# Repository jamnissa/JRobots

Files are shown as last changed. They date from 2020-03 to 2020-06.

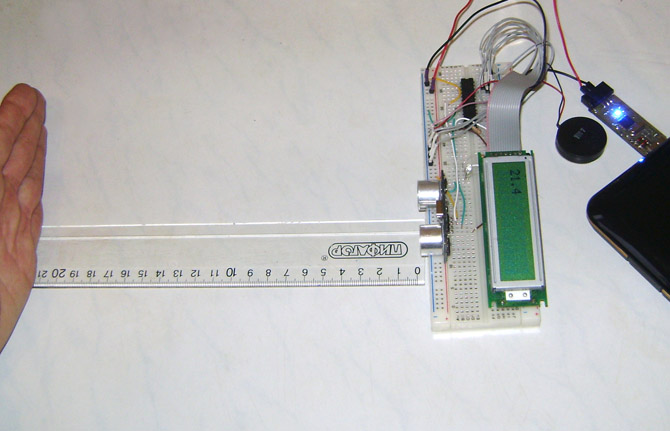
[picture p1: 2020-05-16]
Trash/21sm.jpg

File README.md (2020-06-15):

### JRobots

#### Структура проекта
- [pcbDocuments](pcbDocuments)
    - [pcbDocuments.dwg](pcbDocuments/pcbDocuments.dwg)
    - [Схема электрическая структурная](pcbDocuments/pdfDocuments/E1.pdf)
    - [Схема электрическая функциональная](pcbDocuments/pdfDocuments/E2.pdf)
    - [Схема электрическая принципиальная](pcbDocuments/pdfDocuments/E3.pdf)
    - [Перечень элементов](pcbDocuments/pdfDocuments/PE3.pdf)
    - [Печатная плата](pcbDocuments/pdfDocuments/PP.pdf)
    - [Сборочный чертеж ячейки](pcbDocuments/pdfDocuments/SB.pdf)
    - [Спецификация](pcbDocuments/pdfDocuments/Spec.pdf)
    - [Сборочный чертеж корпуса](pcbDocuments/pdfDocuments/SB_corpus.pdf)
    - [Спецификация 2](pcbDocuments/pdfDocuments/Spec_corpus.pdf)
    - [Алгоритм](pcbDocuments/pdfDocuments/Algoritm.pdf)
    - [Схема сборки](pcbDocuments/pdfDocuments/Sborka.pdf)
    - [Исследовательский лист](pcbDocuments/pdfDocuments/Search.pdf)
    - [Исследовательский лист2](pcbDocuments/pdfDocuments/Search2.pdf)

- [pcbBoard](pcbBoard)
    - [Robot.PrjPcb](pcbBoard/Robot.PrjPcb)
    - [Schematic.SchDoc](pcbBoard/Schematic.SchDoc)
    - [PcbBoard.PcbDoc](pcbBoard/PcbBoard_last3.PcbDoc)
    
- [pcbCase](pcbCase)
    - [ball.ipt](pcbCase/ball/ball.iam)
    - [battery case.ipt](pcbCase/case18650/case18650.ipt)
    - [fixation for motor.ipt](pcbCase/soporte_plastico/soporte_plastico.ipt)
    - [lidar.ipt](pcbCase/lidar/lidar.ipt)
    - [wheel.ipt](pcbCase/wheel/Wheel.ipt)
    - [motor.ipt](pcbCase/motor/motor.ipt)
    - [sborka](pcbCase/pcbCase/sborka.iam)

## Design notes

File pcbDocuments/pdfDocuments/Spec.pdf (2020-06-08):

Инв. №подл Подп. и Дата Взам.инв.№ Инв.№ дубл. Подп. и Дата Справ № Перв. примен. Изм. Лист № докум. Лит. Листов МГТУ им. Н.Э.Баумана Кафедра ИУ4 Группа ИУ4-81Б Лист Робот

-транспортер Спецификация Подпись | Дата Разраб. Пров. Реценз. Н.контр. Утв. | Исабаева Ж. | ИУ4.11.03.03.20.81.06.005 СП
1 | 2 | Инв. №подл Подп. и Дата Взам.инв.№ Инв.№ дубл. Подп. и Дата Справ № Перв. примен. | Изм. | Лист | № докум. | Подпись | Дата | Лист
2 ИУ4.11.03.03.20.81.06.005 СП Копировал | Формат A4 | Копировал | Формат A4

Форм. Зона

## Поз. Обозначение Наименование

Кол. Примечание ИУ4.11.03.03.20.81.06.004 Печатная плата Документация A2 Сборочный чертеж ячейки 1 A2 ИУ4.11.03.03.20.81.06.001

Э1 | Схема электрическая структурная A1 | ИУ4.11.03.03.20.81.06.003
Э3 | Схема электрическая принципиальная A4 | ИУ4.11.03.03.20.81.06.003 ПЭ3 | Перечень элементов A2 | ИУ4.11.03.03.20.81.06.004 | Чертеж печатной платы

1

1

1

1

1

Форм. Зона

## Поз. Обозначение Наименование

Кол. Примечание

1

1 | C8-C13,C16,C19 | Светодиод TO-2013BC, 0805 CC2541 BluetoothмодульJDY-08 STM32F103C8T6, [LQFP-48] | VD1 DD2
1 Светодиоды Микросхемы | DD1
1 PH2.0-2Вилка прямая на плату | 1 | XP1 Разъемы PLD6 Вилка прямая на плату | XP2 TB6612FNG [SSOP-24] | DD3 AMS1117-3.3, [SOT-223] | DA1 AMS1117-5, [SOT-223] | DA2
1 PH2.0-4Вилка прямая на плату | XP3 PH1.5-6,Вилка прямая на плату | 2 | XP4,XP5 Кнопка с фиксацией PS700L | SW1 Переключатели Кнопка тактовая KLS7-TS6601 | SW2 Дроссель подавления ЭМП, | 1 | L1 Катушки индуктивности

1

1

1

1

1

1 BLM21BD182SN1D,0805 Копировал | Формат A4 HC-49SM, 8МГц | 1 | ZQ1 Кварцевые резонаторы Кер.ЧИП конд.0,1мкФ,50
В,0805 | 11 | C1,C3,C5, Конденсаторы ECAP SMD 220мкФ,16
В Кер.ЧИП конд.22пФ,250 | 4
В,0805 В,0805 Кер.ЧИП конд.1мкФ,16 | 2 | C2,C4,C14,C18 C6,C7 C15 C17
В,0805 Кер.ЧИП конд.2,2мкФ.16 | 1

1

3 ЧИП резистор 4,7кОм,0805 2 1 1 1 | R4-R6 Биполярный транзистор PNP, R2,R3 ЧИП резистор 4,7кОм, 0805 VT1 Транзисторы SOT-23 Пьезоэлектрический излучатель BQ1 Преобразователи пассивный HPM14A, 5 R1 Резисторы ЧИП резистор 1кОм,0805

В Детали Прочие изделия ИУ4.11.03.03.20.81.06.005 СБ Артемьев Б.В. Сергеева М.Д.

ВЫПОЛНЕНО В СТУДЕНЧЕСКОЙ ВЕРСИИ ПРОГРАММЫ AUTODESK ВЫПОЛНЕНО В СТУДЕНЧЕСКОЙ ВЕРСИИ ПРОГРАММЫ AUTODESK

ВЫПОЛНЕНО В СТУДЕНЧЕСКОЙ ВЕРСИИ ПРОГРАММЫ AUTODESK ВЫПОЛНЕНО В СТУДЕНЧЕСКОЙ ВЕРСИИ ПРОГРАММЫ AUTODESK

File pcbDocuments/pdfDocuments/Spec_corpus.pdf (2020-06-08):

Инв. №подл Подп. и Дата Взам.инв.№ Инв.№ дубл. Подп. и Дата Справ № Перв. примен. Изм. Лист № докум. Лит. Листов МГТУ им. Н.Э.Баумана Кафедра ИУ4 Группа ИУ4-81Б Лист Робот

-транспортер Спецификация 2 Подпись | Дата Разраб. Пров. Реценз. Н.контр. Утв. | Исабаева Ж. | ИУ4.11.03.03.20.81.06.006СП
1 | 2 | Инв. №подл Подп. и Дата Взам.инв.№ Инв.№ дубл. Подп. и Дата Справ № Перв. примен. | Изм. | Лист | № докум. | Подпись | Дата | Лист
2 ИУ4.11.03.03.20.81.06.006СП Копировал | Формат A4 | Копировал | Формат A4

Форм. Зона

## Поз. Обозначение Наименование

Кол. Примечание Детали ИУ4.11.03.03.20.81.06.004 Печатная плата Документация A2 ИУ4.11.03.03.20.81.06.007 СБ Сборочный чертеж устройства 1 A2 ИУ4.11.03.03.20.81.06.001

Э1 | Схема электрическая структурная A1 | ИУ4.11.03.03.20.81.06.003
ИУ4.11.03.03.20.81.06.003 ПЭ3 ИУ4.11.03.03.20.81.06.004 Э3 | Схема электрическая принципиальная A4 Перечень элементов A2 Чертеж печатной платы | 1
| | 1

1

1 Прочие изделия

1 2 | Кронштейн для двигателя Инкрементный энкодер ЭлектродвигательGA12-N20 | 1
34 | | 1
| | 2 Верхняя крышка Нижняя крышка Верхнее основание Колесо 12
7 | 2
8 | 2

9

Форм. Зона

## Поз. Обозначение Наименование

Кол. Примечание

1

5 | 1618

1

6 | Шаровая опора Pololu 3/8" | 2 10 | Батарейный отсек 2х18650 | 1 Стойка для печатных плат, HTP-325 11 | Винт с круглой головкой
4 1213 | Лидар TF-mini | Винт с потайной головкой

8

7 | 15 15 Стойка для печатных плат, HTS-325 14 | 1 Кронштейн для лидара | M3x10 M2x4 Винт с круглой головкой | 2 17 | Винт с потайной головкой
8 M2x5 19 | Гайка M2 | 14 M2x10 A2 | ИУ4.11.03.03.20.81.06.005 СБ | Сборочный чертеж ячейки | 1 Артемьев Б.В. Сергеева М.Д.

ВЫПОЛНЕНО В СТУДЕНЧЕСКОЙ ВЕРСИИ ПРОГРАММЫ AUTODESK ВЫПОЛНЕНО В СТУДЕНЧЕСКОЙ ВЕРСИИ ПРОГРАММЫ AUTODESK

ВЫПОЛНЕНО В СТУДЕНЧЕСКОЙ ВЕРСИИ ПРОГРАММЫ AUTODESK ВЫПОЛНЕНО В СТУДЕНЧЕСКОЙ ВЕРСИИ ПРОГРАММЫ AUTODESK

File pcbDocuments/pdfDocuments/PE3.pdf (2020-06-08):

Инв. №подл Подп. и Дата Взам.инв.№ Инв.№ дубл. Подп. и Дата Справ № Перв. примен. Изм. Лист № докум.

ЗонаПоз. Обозна
-чение | Обозначение

# Кол. Примечание Лит. Листов 1 МГТУ им. Н.Э.Баумана Кафедра ИУ4 Группа ИУ4-81Б Лист Робот

-транспортер Перечень элементов Подпись | Дата Разраб. Пров. Реценз. Н.контр. Утв. | ИУ4.11.03.03.20.81.06.003 ПЭ

3

1 | 2 | Инв. №подл Подп. и Дата Взам.инв.№ Инв.№ дубл. Подп. и Дата Справ № Перв. примен. | Зона | Поз. Обозна
-чение | Обозначение

Кол. Примечание Изм. Лист № докум. Подпись Дата Лист

## 2 ИУ4.11.03.03.20.81.06.003 ПЭ

3 Светодиод желтый TO-2013BC-MYF, 0805, КНР CC2541 Bluetoothмодуль JDY-08, Texas Instruments STM32F103C8T6,32-Бит,Cortex-M3, 72 МГц, | VD1 DD2 | Светодиоды Микросхемы DD1 | 1 Конденсаторы Кер.ЧИП конд.0,1мкФ±10% 50

В-X7R-0805 EGRM21BR71H104K, Murata Manufacturing ECAP SMD 220мкФ±20%-16 В-Y5V-6,3x7,7 C1,C3,C5 C2,C4,C14 C18

1 XP1 | PH2.0-2, Вилка прямая на плату 2.0мм, КНР | 1 Разъемы XP2 | PLD6 Вилка прямая на плату, Тайвань Копировал | Формат A4 | Копировал | Формат A4 Копировал | Формат A4

1 Кер.ЧИП конд.22пФ±5% 250

Кер.ЧИП конд.2,2мкФ±10% 16 В-C0G-0805 GRM21A5C2E220J, Murata Manufacturing C6,C7 C15 | 2 Кер.ЧИП конд. 1мкФ±10% 16
В-Y5V-0805,Тайвань | 1 64 КБ Flash [LQFP-48], Швейцария DD3 | TB6612FNG [SSOP-24],Toshiba,Япония | 1 DA1 | AMS1117-3.3,Линейный стабилизатор[SOT-223],3.3
AMS1117-5,Линейный стабилизатор [SOT-223],5 В,КНР | 1 DA2
В,КНР | 1
1 XP3 | PH2.0-4, Вилка прямая на плату 2.0мм, КНР | XP4,XP5 | PH1.5-6, Вилка прямая на плату 1.5мм, КНР | 2 BQ1 | Пьезоэлектрический излучатель пассивный HPM14A, 5
В | 1 Кварцевые резонаторы | SW1 | Кнопка с фиксацией PS700L, КНР | 1 Переключатели C17 | SW2 | Кнопка тактовая KLS7-TS6601-5.0 | 1 ZQ1 | HC-49SM 8МГц,КНР | 1 L1 | Дроссель подавления ЭМП,BLM21BD182SN1D,1.8кОм,0805 | 1 Катушки индуктивности C8-C13, C16,C19 | 114
В-X7R-0805 | 1
3 R1 | ЧИП резистор 4,7кОм± 5%-0,125-0805, Тайвань | 1 Резисторы R2,R3 | ЧИП резистор 1кОм± 5%-0,125-0805, Тайвань | 2 R4-R6 | ЧИП резистор 4,7кОм± 5%-0,125-0805, Тайвань
1 VT1 | Биполярный транзистор PNP SOT-23,KTC9012S-H-RTK/P | 1 Транзисторы Преобразователи Исабаева Ж. Сергеева М.Д. Артемьев Б.В. ВЫПОЛНЕНО В СТУДЕНЧЕСКОЙ ВЕРСИИ ПРОГРАММЫ AUTODESK | ВЫПОЛНЕНО В СТУДЕНЧЕСКОЙ ВЕРСИИ ПРОГРАММЫ AUTODESK

ВЫПОЛНЕНО В СТУДЕНЧЕСКОЙ ВЕРСИИ ПРОГРАММЫ AUTODESK ВЫПОЛНЕНО В СТУДЕНЧЕСКОЙ ВЕРСИИ ПРОГРАММЫ AUTODESK

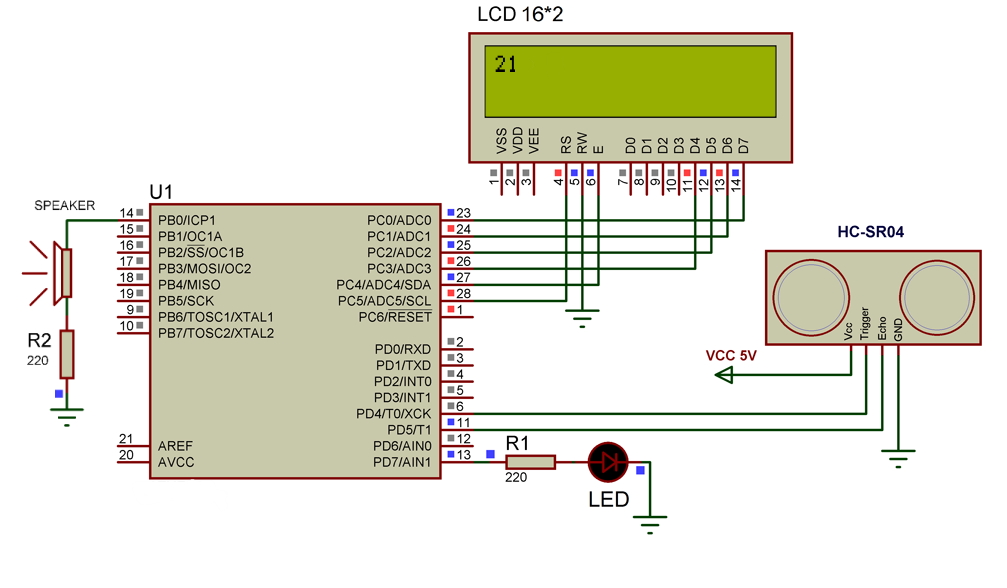
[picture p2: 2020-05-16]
Trash/proteus.jpg

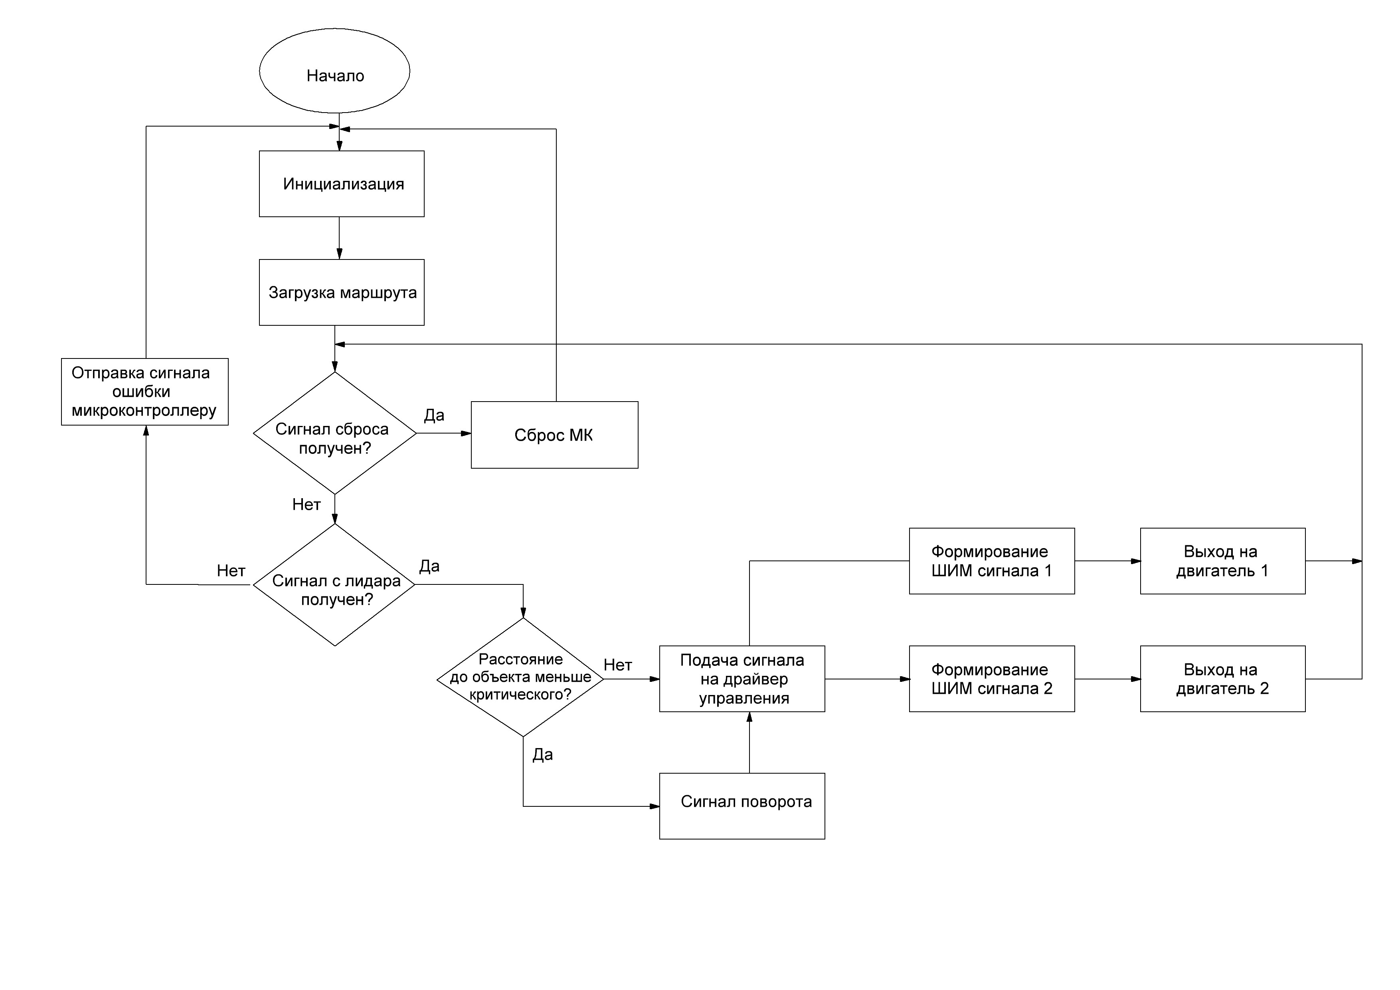
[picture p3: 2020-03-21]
Trash/алгоритм.JPG

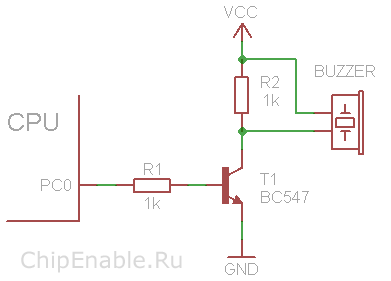
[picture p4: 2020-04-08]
Trash/buzzer3.png

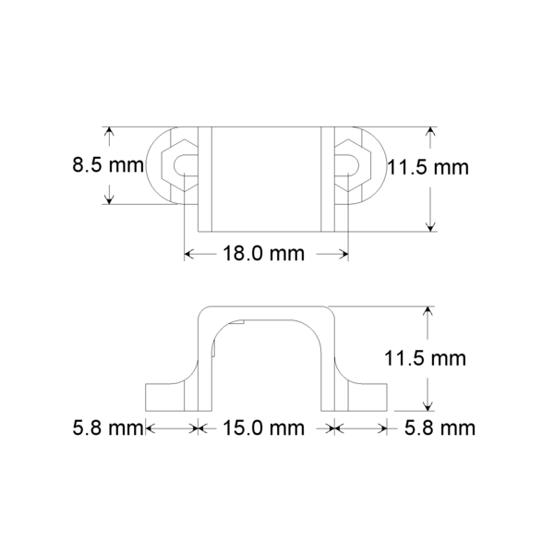
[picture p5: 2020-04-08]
Trash/19a99f53-5988-11e1-8759-001d60b84a57_5c161ac9-bea5-11e1-bbff-001d60b84a57.resize1.jpeg

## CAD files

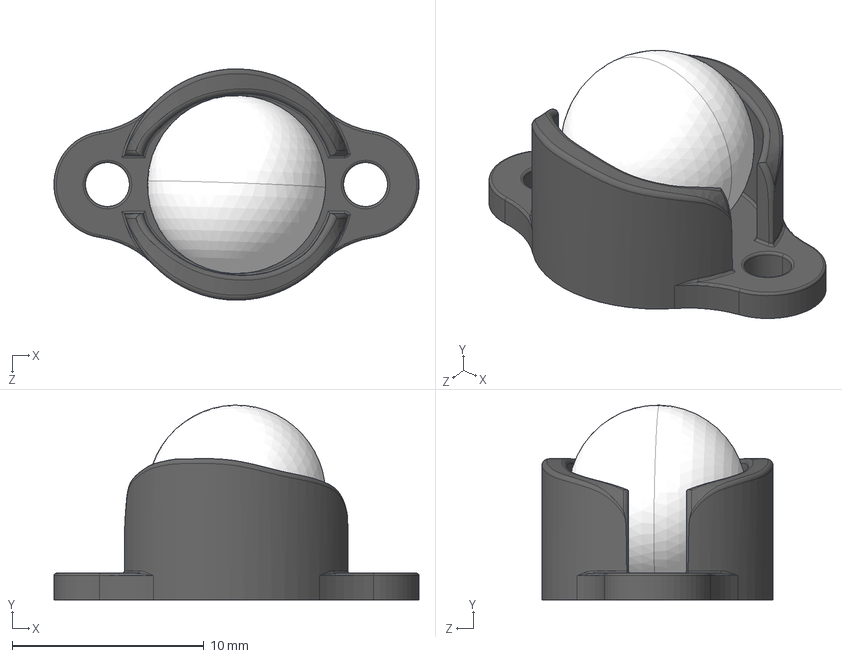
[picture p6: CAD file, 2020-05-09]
pcbCase/ball/ball.STEP
19.0 x 10.2 x 12.1 mm
base
ball

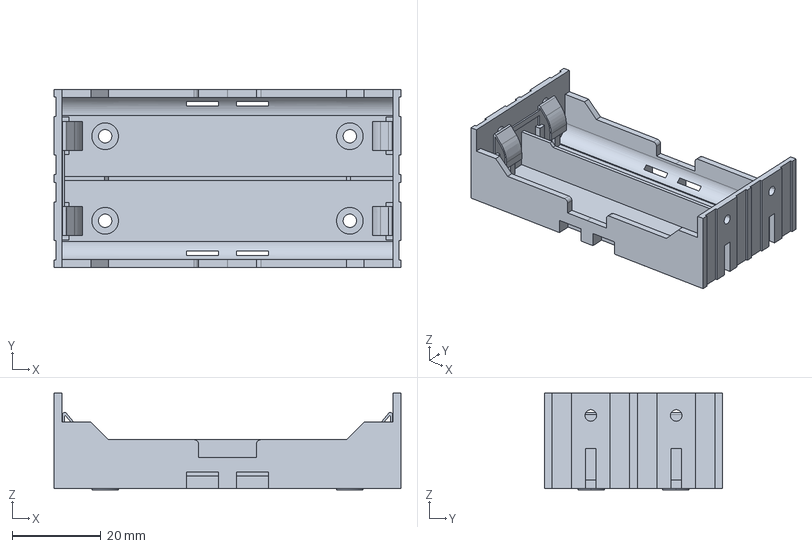
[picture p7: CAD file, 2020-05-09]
pcbCase/case18650/case18650.stp
78.0 x 40.0 x 21.8 mm

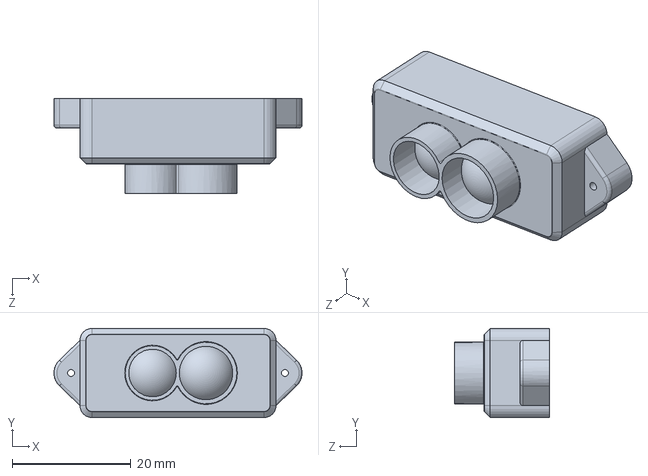
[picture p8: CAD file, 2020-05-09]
pcbCase/lidar/mini_Lidar.SLDPRT
41.7 x 15.0 x 16.0 mm

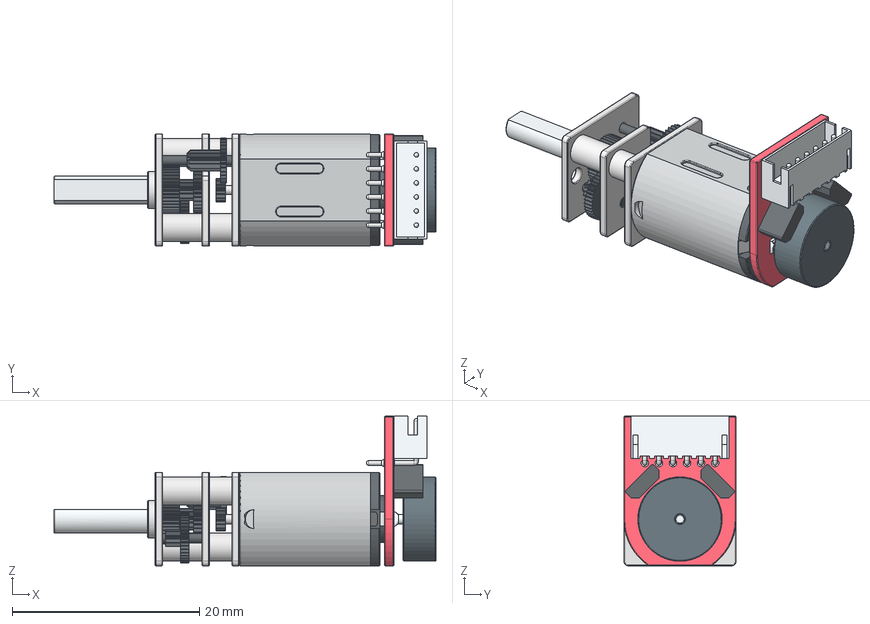
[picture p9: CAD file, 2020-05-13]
pcbCase/motor/motor.stp
40.8 x 12.0 x 16.0 mm
motor_1
motor_1_1
motor_2
motor_3
motor_4
motor_5
motor_6
motor_7
motor_8
motor_9
motor_10
motor_11
motor_12
motor_13
motor_14
motor_15
motor_16
motor_17
motor_18
motor_19
motor_20
motor_21
motor_22
motor_23
motor_24
motor_25
motor_26
motor_27
motor_28
motor_29
motor_30
motor_31
motor_32
motor_33
motor_34
motor_35
motor_36

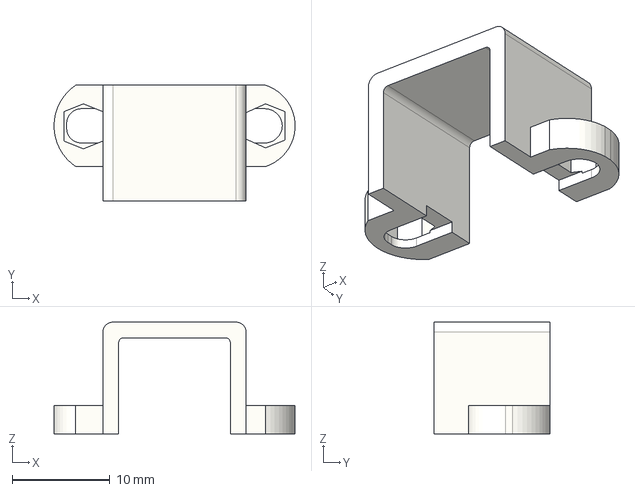
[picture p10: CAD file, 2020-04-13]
pcbCase/soporte_plastico/soporte_plastico.step
24.6 x 11.8 x 11.4 mm

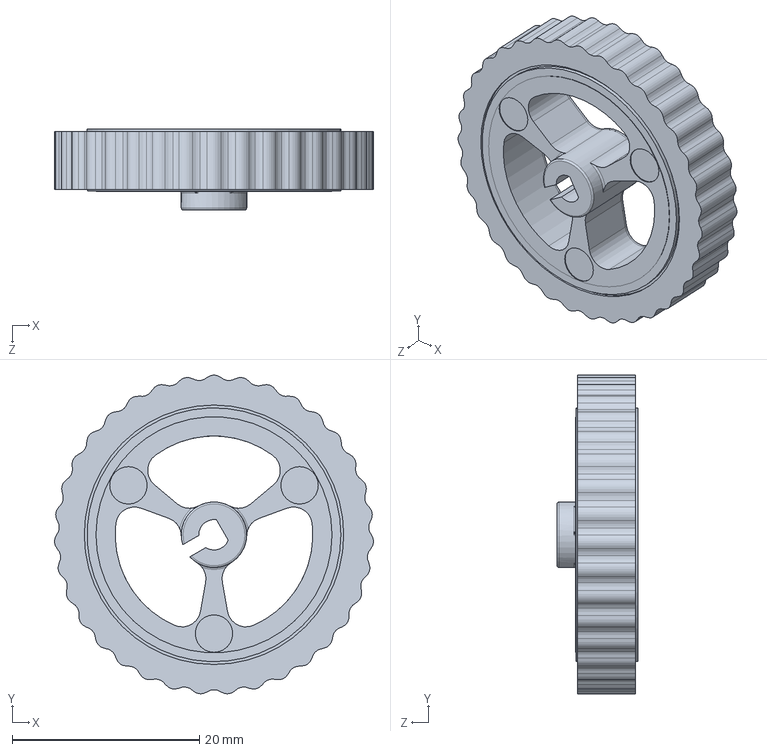
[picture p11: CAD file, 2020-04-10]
pcbCase/wheel/Wheel.SLDPRT
34.1 x 34.0 x 8.65 mm

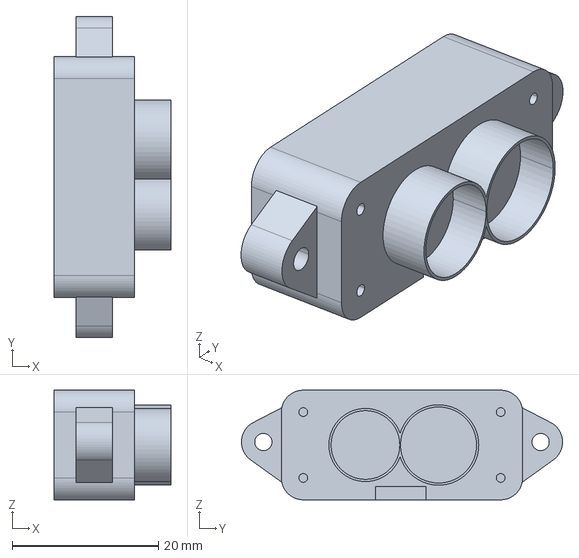
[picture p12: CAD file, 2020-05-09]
pcbCase/lidar/lidar.stp
16.0 x 43.9 x 15.0 mm

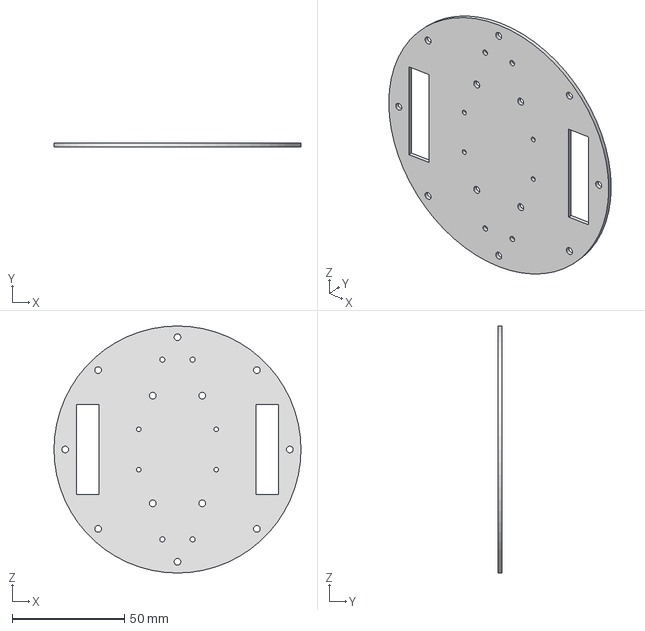
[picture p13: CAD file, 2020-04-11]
pcbCase/pcbCase/pcbCase.stp
110.0 x 1.60 x 110.0 mm

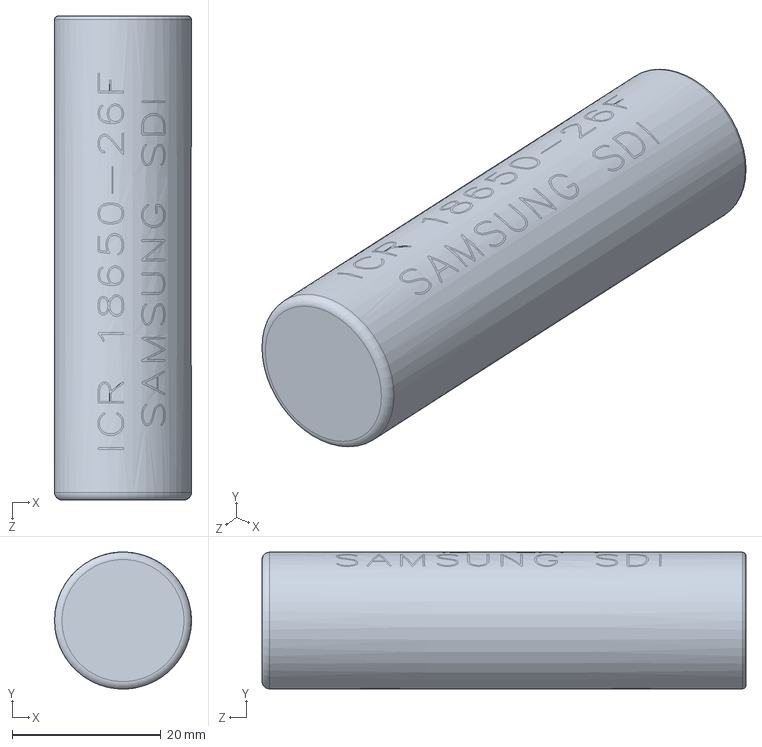
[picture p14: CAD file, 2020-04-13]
pcbCase/case18650/18650.SLDPRT
18.4 x 18.4 x 65.0 mm

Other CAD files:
pcbCase/pcbCase/caseTop.dwg
pcbDocuments/pcbDocuments.dwg
pcbCase/pcbCase/pcbCase_last.dwg
pcbDocuments/pcbDoc.dwg
pcbCase/case18650/BatteryCase.dwg
pcbCase/pcbCase/caseBottom.dwg
pcbCase/pcbCase/Board.dwg
pcbCase/OldVersions/sborka2.0001.dwg
pcbCase/pcbCase/OldVersions/caseBottom.0002.dwg
pcbCase/Board/0805LED-red.ipt
pcbCase/Board/B6B-ZR.ipt
pcbCase/Board/BQ1.iam
pcbCase/Board/BQ2.iam
pcbCase/Board/Board.iam
pcbCase/Board/C1.iam
pcbCase/Board/C10.iam
pcbCase/Board/C11.iam
pcbCase/Board/C12.iam
pcbCase/Board/C13.iam
pcbCase/Board/C14.iam
pcbCase/Board/C15.iam
pcbCase/Board/C16.iam
pcbCase/Board/C17.iam
pcbCase/Board/C18.iam
pcbCase/Board/C19.iam
pcbCase/Board/C2.iam
pcbCase/Board/C3.iam
pcbCase/Board/C4.iam
pcbCase/Board/C5.iam
pcbCase/Board/C6.iam
pcbCase/Board/C7.iam
pcbCase/Board/C8.iam
pcbCase/Board/C9.iam
pcbCase/Board/DA1.iam
pcbCase/Board/DA2.iam
pcbCase/Board/DD1.iam
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

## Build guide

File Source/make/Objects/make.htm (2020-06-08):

# Static Call Graph for image .\Objects\make.axf

#<CALLGRAPH># ARM Linker, 5060750: Last Updated: Sun Jun 07 21:56:51 2020

### Maximum Stack Usage = 96 bytes + Unknown(Functions without stacksize, Cycles, Untraceable Function Pointers)

### Call chain for Maximum Stack Depth:

TIM4_IRQHandler ⇒ encoderRead ⇒ __aeabi_dmul

### Functions with no stack information

- __user_initial_stackheap

### Mutually Recursive functions

- NMI_Handler ⇒ NMI_Handler
- HardFault_Handler ⇒ HardFault_Handler
- MemManage_Handler ⇒ MemManage_Handler
- BusFault_Handler ⇒ BusFault_Handler
- UsageFault_Handler ⇒ UsageFault_Handler
- SVC_Handler ⇒ SVC_Handler
- DebugMon_Handler ⇒ DebugMon_Handler
- PendSV_Handler ⇒ PendSV_Handler
- SysTick_Handler ⇒ SysTick_Handler
- ADC1_2_IRQHandler ⇒ ADC1_2_IRQHandler

### Function Pointers

- ADC1_2_IRQHandler from startup_stm32f10x_md.o(.text) referenced from startup_stm32f10x_md.o(RESET)
- BusFault_Handler from startup_stm32f10x_md.o(.text) referenced from startup_stm32f10x_md.o(RESET)
- CAN1_RX1_IRQHandler from startup_stm32f10x_md.o(.text) referenced from startup_stm32f10x_md.o(RESET)
- CAN1_SCE_IRQHandler from startup_stm32f10x_md.o(.text) referenced from startup_stm32f10x_md.o(RESET)
- DMA1_Channel1_IRQHandler from startup_stm32f10x_md.o(.text) referenced from startup_stm32f10x_md.o(RESET)
- DMA1_Channel2_IRQHandler from startup_stm32f10x_md.o(.text) referenced from startup_stm32f10x_md.o(RESET)
- DMA1_Channel3_IRQHandler from startup_stm32f10x_md.o(.text) referenced from startup_stm32f10x_md.o(RESET)
- DMA1_Channel4_IRQHandler from startup_stm32f10x_md.o(.text) referenced from startup_stm32f10x_md.o(RESET)
- DMA1_Channel5_IRQHandler from startup_stm32f10x_md.o(.text) referenced from startup_stm32f10x_md.o(RESET)
- DMA1_Channel6_IRQHandler from startup_stm32f10x_md.o(.text) referenced from startup_stm32f10x_md.o(RESET)
- DMA1_Channel7_IRQHandler from startup_stm32f10x_md.o(.text) referenced from startup_stm32f10x_md.o(RESET)
- DebugMon_Handler from startup_stm32f10x_md.o(.text) referenced from startup_stm32f10x_md.o(RESET)
- EXTI0_IRQHandler from startup_stm32f10x_md.o(.text) referenced from startup_stm32f10x_md.o(RESET)
- EXTI15_10_IRQHandler from startup_stm32f10x_md.o(.text) referenced from startup_stm32f10x_md.o(RESET)
- EXTI1_IRQHandler from startup_stm32f10x_md.o(.text) referenced from startup_stm32f10x_md.o(RESET)
- EXTI2_IRQHandler from startup_stm32f10x_md.o(.text) referenced from startup_stm32f10x_md.o(RESET)
- EXTI3_IRQHandler from startup_stm32f10x_md.o(.text) referenced from startup_stm32f10x_md.o(RESET)
- EXTI4_IRQHandler from startup_stm32f10x_md.o(.text) referenced from startup_stm32f10x_md.o(RESET)
- EXTI9_5_IRQHandler from startup_stm32f10x_md.o(.text) referenced from startup_stm32f10x_md.o(RESET)
- FLASH_IRQHandler from startup_stm32f10x_md.o(.text) referenced from startup_stm32f10x_md.o(RESET)
- HardFault_Handler from startup_stm32f10x_md.o(.text) referenced from startup_stm32f10x_md.o(RESET)
- I2C1_ER_IRQHandler from startup_stm32f10x_md.o(.text) referenced from startup_stm32f10x_md.o(RESET)
- I2C1_EV_IRQHandler from startup_stm32f10x_md.o(.text) referenced from startup_stm32f10x_md.o(RESET)
- I2C2_ER_IRQHandler from startup_stm32f10x_md.o(.text) referenced from startup_stm32f10x_md.o(RESET)
- I2C2_EV_IRQHandler from startup_stm32f10x_md.o(.text) referenced from startup_stm32f10x_md.o(RESET)
- MemManage_Handler from startup_stm32f10x_md.o(.text) referenced from startup_stm32f10x_md.o(RESET)
- NMI_Handler from startup_stm32f10x_md.o(.text) referenced from startup_stm32f10x_md.o(RESET)
- PVD_IRQHandler from startup_stm32f10x_md.o(.text) referenced from startup_stm32f10x_md.o(RESET)
- PendSV_Handler from startup_stm32f10x_md.o(.text) referenced from startup_stm32f10x_md.o(RESET)
- RCC_IRQHandler from startup_stm32f10x_md.o(.text) referenced from startup_stm32f10x_md.o(RESET)
- RTCAlarm_IRQHandler from startup_stm32f10x_md.o(.text) referenced from startup_stm32f10x_md.o(RESET)
- RTC_IRQHandler from startup_stm32f10x_md.o(.text) referenced from startup_stm32f10x_md.o(RESET)
- Reset_Handler from startup_stm32f10x_md.o(.text) referenced from startup_stm32f10x_md.o(RESET)
- SPI1_IRQHandler from startup_stm32f10x_md.o(.text) referenced from startup_stm32f10x_md.o(RESET)
- SPI2_IRQHandler from startup_stm32f10x_md.o(.text) referenced from startup_stm32f10x_md.o(RESET)
- SVC_Handler from startup_stm32f10x_md.o(.text) referenced from startup_stm32f10x_md.o(RESET)
- SysTick_Handler from startup_stm32f10x_md.o(.text) referenced from startup_stm32f10x_md.o(RESET)
- SystemInit from system_stm32f10x.o(i.SystemInit) referenced from startup_stm32f10x_md.o(.text)
- TAMPER_IRQHandler from startup_stm32f10x_md.o(.text) referenced from startup_stm32f10x_md.o(RESET)
- TIM1_BRK_IRQHandler from startup_stm32f10x_md.o(.text) referenced from startup_stm32f10x_md.o(RESET)
- TIM1_CC_IRQHandler from startup_stm32f10x_md.o(.text) referenced from startup_stm32f10x_md.o(RESET)
- TIM1_TRG_COM_IRQHandler from startup_stm32f10x_md.o(.text) referenced from startup_stm32f10x_md.o(RESET)
- TIM1_UP_IRQHandler from startup_stm32f10x_md.o(.text) referenced from startup_stm32f10x_md.o(RESET)
- TIM2_IRQHandler from startup_stm32f10x_md.o(.text) referenced from startup_stm32f10x_md.o(RESET)
- TIM3_IRQHandler from startup_stm32f10x_md.o(.text) referenced from startup_stm32f10x_md.o(RESET)
- TIM4_IRQHandler from jrobot.o(i.TIM4_IRQHandler) referenced from startup_stm32f10x_md.o(RESET)
- USART1_IRQHandler from startup_stm32f10x_md.o(.text) referenced from startup_stm32f10x_md.o(RESET)
- USART2_IRQHandler from startup_stm32f10x_md.o(.text) referenced from startup_stm32f10x_md.o(RESET)
- USART3_IRQHandler from startup_stm32f10x_md.o(.text) referenced from startup_stm32f10x_md.o(RESET)
- USBWakeUp_IRQHandler from startup_stm32f10x_md.o(.text) referenced from startup_stm32f10x_md.o(RESET)
- USB_HP_CAN1_TX_IRQHandler from startup_stm32f10x_md.o(.text) referenced from startup_stm32f10x_md.o(RESET)
- USB_LP_CAN1_RX0_IRQHandler from startup_stm32f10x_md.o(.text) referenced from startup_stm32f10x_md.o(RESET)
- UsageFault_Handler from startup_stm32f10x_md.o(.text) referenced from startup_stm32f10x_md.o(RESET)
- WWDG_IRQHandler from startup_stm32f10x_md.o(.text) referenced from startup_stm32f10x_md.o(RESET)
- __main from __main.o(!!!main) referenced from startup_stm32f10x_md.o(.text)

### Global Symbols

__main (Thumb, 8 bytes, Stack size 0 bytes, __main.o(!!!main))

[Calls]

- >> __scatterload
- >> __rt_entry

__scatterload (Thumb, 0 bytes, Stack size unknown bytes, __scatter.o(!!!scatter))

[Called By]

- >> __main

__scatterload_rt2 (Thumb, 44 bytes, Stack size unknown bytes, __scatter.o(!!!scatter), UNUSED)

[Calls]

- >> __rt_entry

__scatterload_rt2_thumb_only (Thumb, 0 bytes, Stack size unknown bytes, __scatter.o(!!!scatter), UNUSED)

__scatterload_null (Thumb, 0 bytes, Stack size unknown bytes, __scatter.o(!!!scatter), UNUSED)

__scatterload_copy (Thumb, 26 bytes, Stack size unknown bytes, __scatter_copy.o(!!handler_copy), UNUSED)

[Calls]

- >> __scatterload_copy

[Called By]

- >> __scatterload_copy

__scatterload_zeroinit (Thumb, 28 bytes, Stack size unknown bytes, __scatter_zi.o(!!handler_zi), UNUSED)

__rt_lib_init (Thumb, 0 bytes, Stack size unknown bytes, libinit.o(.ARM.Collect$$libinit$$00000000))

[Called By]

- >> __rt_entry_li

__rt_lib_init_alloca_1 (Thumb, 0 bytes, Stack size unknown bytes, libinit2.o(.ARM.Collect$$libinit$$0000002E))

__rt_lib_init_argv_1 (Thumb, 0 bytes, Stack size unknown bytes, libinit2.o(.ARM.Collect$$libinit$$0000002C))

__rt_lib_init_atexit_1 (Thumb, 0 bytes, Stack size unknown bytes, libinit2.o(.ARM.Collect$$libinit$$0000001B))

__rt_lib_init_clock_1 (Thumb, 0 bytes, Stack size unknown bytes, libinit2.o(.ARM.Collect$$libinit$$00000021))

__rt_lib_init_cpp_1 (Thumb, 0 bytes, Stack size unknown bytes, libinit2.o(.ARM.Collect$$libinit$$00000032))

__rt_lib_init_exceptions_1 (Thumb, 0 bytes, Stack size unknown bytes, libinit2.o(.ARM.Collect$$libinit$$00000030))

__rt_lib_init_fp_1 (Thumb, 0 bytes, Stack size unknown bytes, libinit2.o(.ARM.Collect$$libinit$$00000002))

__rt_lib_init_fp_trap_1 (Thumb, 0 bytes, Stack size unknown bytes, libinit2.o(.ARM.Collect$$libinit$$0000001F))

__rt_lib_init_getenv_1 (Thumb, 0 bytes, Stack size unknown bytes, libinit2.o(.ARM.Collect$$libinit$$00000023))

__rt_lib_init_heap_1 (Thumb, 0 bytes, Stack size unknown bytes, libinit2.o(.ARM.Collect$$libinit$$0000000A))

__rt_lib_init_lc_collate_1 (Thumb, 0 bytes, Stack size unknown bytes, libinit2.o(.ARM.Collect$$libinit$$00000011))

__rt_lib_init_lc_ctype_1 (Thumb, 0 bytes, Stack size unknown bytes, libinit2.o(.ARM.Collect$$libinit$$00000013))

__rt_lib_init_lc_monetary_1 (Thumb, 0 bytes, Stack size unknown bytes, libinit2.o(.ARM.Collect$$libinit$$00000015))

__rt_lib_init_lc_numeric_1 (Thumb, 0 bytes, Stack size unknown bytes, libinit2.o(.ARM.Collect$$libinit$$00000017))

__rt_lib_init_lc_time_1 (Thumb, 0 bytes, Stack size unknown bytes, libinit2.o(.ARM.Collect$$libinit$$00000019))

__rt_lib_init_preinit_1 (Thumb, 0 bytes, Stack size unknown bytes, libinit2.o(.ARM.Collect$$libinit$$00000004))

__rt_lib_init_rand_1 (Thumb, 0 bytes, Stack size unknown bytes, libinit2.o(.ARM.Collect$$libinit$$0000000E))

__rt_lib_init_return (Thumb, 0 bytes, Stack size unknown bytes, libinit2.o(.ARM.Collect$$libinit$$00000033))

__rt_lib_init_signal_1 (Thumb, 0 bytes, Stack size unknown bytes, libinit2.o(.ARM.Collect$$libinit$$0000001D))

__rt_lib_init_stdio_1 (Thumb, 0 bytes, Stack size unknown bytes, libinit2.o(.ARM.Collect$$libinit$$00000025))

__rt_lib_init_user_alloc_1 (Thumb, 0 bytes, Stack size unknown bytes, libinit2.o(.ARM.Collect$$libinit$$0000000C))

__rt_lib_shutdown (Thumb, 0 bytes, Stack size unknown bytes, libshutdown.o(.ARM.Collect$$libshutdown$$00000000))

[Called By]

- >> __rt_exit_ls

__rt_lib_shutdown_cpp_1 (Thumb, 0 bytes, Stack size unknown bytes, libshutdown2.o(.ARM.Collect$$libshutdown$$00000002))

__rt_lib_shutdown_fp_trap_1 (Thumb, 0 bytes, Stack size unknown bytes, libshutdown2.o(.ARM.Collect$$libshutdown$$00000007))

__rt_lib_shutdown_heap_1 (Thumb, 0 bytes, Stack size unknown bytes, libshutdown2.o(.ARM.Collect$$libshutdown$$0000000F))

__rt_lib_shutdown_return (Thumb, 0 bytes, Stack size unknown bytes, libshutdown2.o(.ARM.Collect$$libshutdown$$00000010))

__rt_lib_shutdown_signal_1 (Thumb, 0 bytes, Stack size unknown bytes, libshutdown2.o(.ARM.Collect$$libshutdown$$0000000A))

__rt_lib_shutdown_stdio_1 (Thumb, 0 bytes, Stack size unknown bytes, libshutdown2.o(.ARM.Collect$$libshutdown$$00000004))

__rt_lib_shutdown_user_alloc_1 (Thumb, 0 bytes, Stack size unknown bytes, libshutdown2.o(.ARM.Collect$$libshutdown$$0000000C))

__rt_entry (Thumb, 0 bytes, Stack size unknown bytes, __rtentry.o(.ARM.Collect$$rtentry$$00000000))

[Called By]

- >> __scatterload_rt2
- >> __main

__rt_entry_presh_1 (Thumb, 0 bytes, Stack size unknown bytes, __rtentry2.o(.ARM.Collect$$rtentry$$00000002))

__rt_entry_sh (Thumb, 0 bytes, Stack size unknown bytes, __rtentry4.o(.ARM.Collect$$rtentry$$00000004))

[Stack]

- Max Depth = 8 + Unknown Stack Size
- Call Chain = __rt_entry_sh ⇒ __user_setup_stackheap

[Calls]

- >> __user_setup_stackheap

__rt_entry_li (Thumb, 0 bytes, Stack size unknown bytes, __rtentry2.o(.ARM.Collect$$rtentry$$0000000A))

[Calls]

- >> __rt_lib_init

__rt_entry_postsh_1 (Thumb, 0 bytes, Stack size unknown bytes, __rtentry2.o(.ARM.Collect$$rtentry$$00000009))

__rt_entry_main (Thumb, 0 bytes, Stack size unknown bytes, __rtentry2.o(.ARM.Collect$$rtentry$$0000000D))

[Stack]

- Max Depth = 8 + Unknown Stack Size
- Call Chain = __rt_entry_main ⇒ exit

[Calls]

- >> exit
- >> main

__rt_entry_postli_1 (Thumb, 0 bytes, Stack size unknown bytes, __rtentry2.o(.ARM.Collect$$rtentry$$0000000C))

__rt_exit (Thumb, 0 bytes, Stack size unknown bytes, rtexit.o(.ARM.Collect$$rtexit$$00000000))

[Called By]

- >> exit

__rt_exit_ls (Thumb, 0 bytes, Stack size unknown bytes, rtexit2.o(.ARM.Collect$$rtexit$$00000003))

[Calls]

- >> __rt_lib_shutdown

__rt_exit_prels_1 (Thumb, 0 bytes, Stack size unknown bytes, rtexit2.o(.ARM.Collect$$rtexit$$00000002))

__rt_exit_exit (Thumb, 0 bytes, Stack size unknown bytes, rtexit2.o(.ARM.Collect$$rtexit$$00000004))

[Calls]

- >> _sys_exit

Reset_Handler (Thumb, 8 bytes, Stack size 0 bytes, startup_stm32f10x_md.o(.text))

NMI_Handler (Thumb, 2 bytes, Stack size 0 bytes, startup_stm32f10x_md.o(.text))

[Calls]

- >> NMI_Handler

[Called By]

- >> NMI_Handler

[Address Reference Count : 1]

- startup_stm32f10x_md.o(RESET)

HardFault_Handler (Thumb, 2 bytes, Stack size 0 bytes, startup_stm32f10x_md.o(.text))

[Calls]

- >> HardFault_Handler

[Called By]

- >> HardFault_Handler

[Address Reference Count : 1]

- startup_stm32f10x_md.o(RESET)

MemManage_Handler (Thumb, 2 bytes, Stack size 0 bytes, startup_stm32f10x_md.o(.text))

[Calls]

- >> MemManage_Handler

[Called By]

- >> MemManage_Handler

[Address Reference Count : 1]

- startup_stm32f10x_md.o(RESET)

BusFault_Handler (Thumb, 2 bytes, Stack size 0 bytes, startup_stm32f10x_md.o(.text))

[Calls]

- >> BusFault_Handler

[Called By]

- >> BusFault_Handler

[Address Reference Count : 1]

- startup_stm32f10x_md.o(RESET)

UsageFault_Handler (Thumb, 2 bytes, Stack size 0 bytes, startup_stm32f10x_md.o(.text))

[Calls]

- >> UsageFault_Handler

[Called By]

- >> UsageFault_Handler

[Address Reference Count : 1]

- startup_stm32f10x_md.o(RESET)

SVC_Handler (Thumb, 2 bytes, Stack size 0 bytes, startup_stm32f10x_md.o(.text))

[Calls]

- >> SVC_Handler

[Called By]

- >> SVC_Handler

[Address Reference Count : 1]

- startup_stm32f10x_md.o(RESET)

DebugMon_Handler (Thumb, 2 bytes, Stack size 0 bytes, startup_stm32f10x_md.o(.text))

[Calls]

- >> DebugMon_Handler

[Called By]

- >> DebugMon_Handler

[Address Reference Count : 1]

- startup_stm32f10x_md.o(RESET)

PendSV_Handler (Thumb, 2 bytes, Stack size 0 bytes, startup_stm32f10x_md.o(.text))

[Calls]

- >> PendSV_Handler

[Called By]

- >> PendSV_Handler

[Address Reference Count : 1]

- startup_stm32f10x_md.o(RESET)

SysTick_Handler (Thumb, 2 bytes, Stack size 0 bytes, startup_stm32f10x_md.o(.text))

[Calls]

- >> SysTick_Handler

[Called By]

- >> SysTick_Handler

[Address Reference Count : 1]

- startup_stm32f10x_md.o(RESET)

ADC1_2_IRQHandler (Thumb, 0 bytes, Stack size 0 bytes, startup_stm32f10x_md.o(.text))

[Calls]

- >> ADC1_2_IRQHandler

[Called By]

- >> ADC1_2_IRQHandler

[Address Reference Count : 1]

- startup_stm32f10x_md.o(RESET)

CAN1_RX1_IRQHandler (Thumb, 0 bytes, Stack size 0 bytes, startup_stm32f10x_md.o(.text))
[Address Reference Count : 1]

- startup_stm32f10x_md.o(RESET)

CAN1_SCE_IRQHandler (Thumb, 0 bytes, Stack size 0 bytes, startup_stm32f10x_md.o(.text))
[Address Reference Count : 1]

- startup_stm32f10x_md.o(RESET)

DMA1_Channel1_IRQHandler (Thumb, 0 bytes, Stack size 0 bytes, startup_stm32f10x_md.o(.text))
[Address Reference Count : 1]

- startup_stm32f10x_md.o(RESET)

DMA1_Channel2_IRQHandler (Thumb, 0 bytes, Stack size 0 bytes, startup_stm32f10x_md.o(.text))
[Address Reference Count : 1]

- startup_stm32f10x_md.o(RESET)

DMA1_Channel3_IRQHandler (Thumb, 0 bytes, Stack size 0 bytes, startup_stm32f10x_md.o(.text))
[Address Reference Count : 1]

- startup_stm32f10x_md.o(RESET)

DMA1_Channel4_IRQHandler (Thumb, 0 bytes, Stack size 0 bytes, startup_stm32f10x_md.o(.text))
[Address Reference Count : 1]

- startup_stm32f10x_md.o(RESET)

DMA1_Channel5_IRQHandler (Thumb, 0 bytes, Stack size 0 bytes, startup_stm32f10x_md.o(.text))
[Address Reference Count : 1]

- startup_stm32f10x_md.o(RESET)

DMA1_Channel6_IRQHandler (Thumb, 0 bytes, Stack size 0 bytes, startup_stm32f10x_md.o(.text))
[Address Reference Count : 1]

- startup_stm32f10x_md.o(RESET)

DMA1_Channel7_IRQHandler (Thumb, 0 bytes, Stack size 0 bytes, startup_stm32f10x_md.o(.text))
[Address Reference Count : 1]

- startup_stm32f10x_md.o(RESET)

EXTI0_IRQHandler (Thumb, 0 bytes, Stack size 0 bytes, startup_stm32f10x_md.o(.text))
[Address Reference Count : 1]

- startup_stm32f10x_md.o(RESET)

EXTI15_10_IRQHandler (Thumb, 0 bytes, Stack size 0 bytes, startup_stm32f10x_md.o(.text))
[Address Reference Count : 1]

- startup_stm32f10x_md.o(RESET)

EXTI1_IRQHandler (Thumb, 0 bytes, Stack size 0 bytes, startup_stm32f10x_md.o(.text))
[Address Reference Count : 1]

- startup_stm32f10x_md.o(RESET)

EXTI2_IRQHandler (Thumb, 0 bytes, Stack size 0 bytes, startup_stm32f10x_md.o(.text))
[Address Reference Count : 1]

- startup_stm32f10x_md.o(RESET)

EXTI3_IRQHandler (Thumb, 0 bytes, Stack size 0 bytes, startup_stm32f10x_md.o(.text))
[Address Reference Count : 1]

- startup_stm32f10x_md.o(RESET)

EXTI4_IRQHandler (Thumb, 0 bytes, Stack size 0 bytes, startup_stm32f10x_md.o(.text))
[Address Reference Count : 1]

- startup_stm32f10x_md.o(RESET)

EXTI9_5_IRQHandler (Thumb, 0 bytes, Stack size 0 bytes, startup_stm32f10x_md.o(.text))
[Address Reference Count : 1]

- startup_stm32f10x_md.o(RESET)

FLASH_IRQHandler (Thumb, 0 bytes, Stack size 0 bytes, startup_stm32f10x_md.o(.text))
[Address Reference Count : 1]

- startup_stm32f10x_md.o(RESET)

I2C1_ER_IRQHandler (Thumb, 0 bytes, Stack size 0 bytes, startup_stm32f10x_md.o(.text))
[Address Reference Count : 1]

- startup_stm32f10x_md.o(RESET)

I2C1_EV_IRQHandler (Thumb, 0 bytes, Stack size 0 bytes, startup_stm32f10x_md.o(.text))
[Address Reference Count : 1]

- startup_stm32f10x_md.o(RESET)

I2C2_ER_IRQHandler (Thumb, 0 bytes, Stack size 0 bytes, startup_stm32f10x_md.o(.text))
[Address Reference Count : 1]

- startup_stm32f10x_md.o(RESET)

I2C2_EV_IRQHandler (Thumb, 0 bytes, Stack size 0 bytes, startup_stm32f10x_md.o(.text))
[Address Reference Count : 1]

- startup_stm32f10x_md.o(RESET)

PVD_IRQHandler (Thumb, 0 bytes, Stack size 0 bytes, startup_stm32f10x_md.o(.text))
[Address Reference Count : 1]

- startup_stm32f10x_md.o(RESET)

RCC_IRQHandler (Thumb, 0 bytes, Stack size 0 bytes, startup_stm32f10x_md.o(.text))
[Address Reference Count : 1]

- startup_stm32f10x_md.o(RESET)

RTCAlarm_IRQHandler (Thumb, 0 bytes, Stack size 0 bytes, startup_stm32f10x_md.o(.text))
[Address Reference Count : 1]

- startup_stm32f10x_md.o(RESET)

RTC_IRQHandler (Thumb, 0 bytes, Stack size 0 bytes, startup_stm32f10x_md.o(.text))
[Address Reference Count : 1]

- startup_stm32f10x_md.o(RESET)

SPI1_IRQHandler (Thumb, 0 bytes, Stack size 0 bytes, startup_stm32f10x_md.o(.text))
[Address Reference Count : 1]

- startup_stm32f10x_md.o(RESET)

SPI2_IRQHandler (Thumb, 0 bytes, Stack size 0 bytes, startup_stm32f10x_md.o(.text))
[Address Reference Count : 1]

- startup_stm32f10x_md.o(RESET)

TAMPER_IRQHandler (Thumb, 0 bytes, Stack size 0 bytes, startup_stm32f10x_md.o(.text))
[Address Reference Count : 1]

- startup_stm32f10x_md.o(RESET)

TIM1_BRK_IRQHandler (Thumb, 0 bytes, Stack size 0 bytes, startup_stm32f10x_md.o(.text))
[Address Reference Count : 1]

- startup_stm32f10x_md.o(RESET)

TIM1_CC_IRQHandler (Thumb, 0 bytes, Stack size 0 bytes, startup_stm32f10x_md.o(.text))
[Address Reference Count : 1]

- startup_stm32f10x_md.o(RESET)

TIM1_TRG_COM_IRQHandler (Thumb, 0 bytes, Stack size 0 bytes, startup_stm32f10x_md.o(.text))
[Address Reference Count : 1]

- startup_stm32f10x_md.o(RESET)

TIM1_UP_IRQHandler (Thumb, 0 bytes, Stack size 0 bytes, startup_stm32f10x_md.o(.text))
[Address Reference Count : 1]

- startup_stm32f10x_md.o(RESET)

TIM2_IRQHandler (Thumb, 0 bytes, Stack size 0 bytes, startup_stm32f10x_md.o(.text))
[Address Reference Count : 1]

- startup_stm32f10x_md.o(RESET)

TIM3_IRQHandler (Thumb, 0 bytes, Stack size 0 bytes, startup_stm32f10x_md.o(.text))
[Address Reference Count : 1]

- startup_stm32f10x_md.o(RESET)

USART1_IRQHandler (Thumb, 0 bytes, Stack size 0 bytes, startup_stm32f10x_md.o(.text))
[Address Reference Count : 1]

- startup_stm32f10x_md.o(RESET)

USART2_IRQHandler (Thumb, 0 bytes, Stack size 0 bytes, startup_stm32f10x_md.o(.text))
[Address Reference Count : 1]

- startup_stm32f10x_md.o(RESET)

USART3_IRQHandler (Thumb, 0 bytes, Stack size 0 bytes, startup_stm32f10x_md.o(.text))
[Address Reference Count : 1]

- startup_stm32f10x_md.o(RESET)

USBWakeUp_IRQHandler (Thumb, 0 bytes, Stack size 0 bytes, startup_stm32f10x_md.o(.text))
[Address Reference Count : 1]

- startup_stm32f10x_md.o(RESET)

USB_HP_CAN1_TX_IRQHandler (Thumb, 0 bytes, Stack size 0 bytes, startup_stm32f10x_md.o(.text))
[Address Reference Count : 1]

- startup_stm32f10x_md.o(RESET)

USB_LP_CAN1_RX0_IRQHandler (Thumb, 0 bytes, Stack size 0 bytes, startup_stm32f10x_md.o(.text))
[Address Reference Count : 1]

- startup_stm32f10x_md.o(RESET)

WWDG_IRQHandler (Thumb, 0 bytes, Stack size 0 bytes, startup_stm32f10x_md.o(.text))
[Address Reference Count : 1]

- startup_stm32f10x_md.o(RESET)

__user_initial_stackheap (Thumb, 0 bytes, Stack size unknown bytes, startup_stm32f10x_md.o(.text))

[Called By]

- >> __user_setup_stackheap

__use_two_region_memory (Thumb, 2 bytes, Stack size 0 bytes, heapauxi.o(.text), UNUSED)

__rt_heap_escrow$2region (Thumb, 2 bytes, Stack size 0 bytes, heapauxi.o(.text), UNUSED)

__rt_heap_expand$2region (Thumb, 2 bytes, Stack size 0 bytes, heapauxi.o(.text), UNUSED)

__user_setup_stackheap (Thumb, 74 bytes, Stack size 8 bytes, sys_stackheap_outer.o(.text))

[Stack]

- Max Depth = 8 + Unknown Stack Size
- Call Chain = __user_setup_stackheap

[Calls]

- >> __user_perproc_libspace
- >> __user_initial_stackheap

[Called By]

- >> __rt_entry_sh

exit (Thumb, 18 bytes, Stack size 8 bytes, exit.o(.text))

[Stack]

- Max Depth = 8 + Unknown Stack Size
- Call Chain = exit

[Calls]

- >> __rt_exit

[Called By]

- >> __rt_entry_main

__user_libspace (Thumb, 8 bytes, Stack size 0 bytes, libspace.o(.text), UNUSED)

__user_perproc_libspace (Thumb, 0 bytes, Stack size 0 bytes, libspace.o(.text))

[Called By]

- >> __user_setup_stackheap

__user_perthread_libspace (Thumb, 0 bytes, Stack size 0 bytes, libspace.o(.text), UNUSED)

_sys_exit (Thumb, 8 bytes, Stack size 0 bytes, sys_exit.o(.text))

[Called By]

- >> __rt_exit_exit

__I$use$semihosting (Thumb, 0 bytes, Stack size 0 bytes, use_no_semi.o(.text), UNUSED)

__use_no_semihosting_swi (Thumb, 2 bytes, Stack size 0 bytes, use_no_semi.o(.text), UNUSED)

__semihosting_library_function (Thumb, 0 bytes, Stack size 8 bytes, indicate_semi.o(.text), UNUSED)

SystemInit (Thumb, 78 bytes, Stack size 8 bytes, system_stm32f10x.o(i.SystemInit))

[Stack]

- Max Depth = 28
- Call Chain = SystemInit ⇒ SetSysClock ⇒ SetSysClockTo72

[Calls]

- >> SetSysClock

[Address Reference Count : 1]

- startup_stm32f10x_md.o(.text)

TIM4_IRQHandler (Thumb, 138 bytes, Stack size 16 bytes, jrobot.o(i.TIM4_IRQHandler))

[Stack]

- Max Depth = 96
- Call Chain = TIM4_IRQHandler ⇒ encoderRead ⇒ __aeabi_dmul

[Calls]

- >> __aeabi_fmul
- >> __aeabi_i2f
- >> __aeabi_f2iz
- >> __aeabi_fadd
- >> motorForward
- >> encoderRead

[Address Reference Count : 1]

- startup_stm32f10x_md.o(RESET)

driverBegin (Thumb, 108 bytes, Stack size 0 bytes, motor.o(i.driverBegin))

[Called By]

- >> motorBegin

encoderLeftBegin (Thumb, 158 bytes, Stack size 0 bytes, motor.o(i.encoderLeftBegin))

[Called By]

- >> main

encoderRead (Thumb, 100 bytes, Stack size 48 bytes, motor.o(i.encoderRead))

[Stack]

- Max Depth = 80
- Call Chain = encoderRead ⇒ __aeabi_dmul

[Calls]

- >> __aeabi_fmul
- >> __aeabi_i2f
- >> __aeabi_fadd
- >> __aeabi_f2d
- >> __aeabi_dmul
- >> __aeabi_d2f

[Called By]

- >> TIM4_IRQHandler

encoderRightBegin (Thumb, 156 bytes, Stack size 0 bytes, motor.o(i.encoderRightBegin))

[Called By]

- >> main

main (Thumb, 26 bytes, Stack size 0 bytes, jrobot.o(i.main))

[Stack]

- Max Depth = 4
- Call Chain = main ⇒ motorBegin

[Calls]

- >> motorBegin
- >> encoderRightBegin
- >> encoderLeftBegin
- >> tim4Begin

[Called By]

- >> __rt_entry_main

motorBegin (Thumb, 12 bytes, Stack size 4 bytes, motor.o(i.motorBegin))

[Stack]

- Max Depth = 4
- Call Chain = motorBegin

[Calls]

- >> pwmBegin
- >> driverBegin

[Called By]

- >> main

motorForward (Thumb, 36 bytes, Stack size 8 bytes, motor.o(i.motorForward))

[Stack]

- Max Depth = 8
- Call Chain = motorForward

[Calls]

- >> motorPwm

[Called By]

- >> TIM4_IRQHandler

motorPwm (Thumb, 10 bytes, Stack size 0 bytes, motor.o(i.motorPwm))

[Called By]

- >> motorForward

pwmBegin (Thumb, 164 bytes, Stack size 0 bytes, motor.o(i.pwmBegin))

[Called By]

- >> motorBegin

tim4Begin (Thumb, 94 bytes, Stack size 0 bytes, jrobot.o(i.tim4Begin))

[Called By]

- >> main

__aeabi_d2f (Thumb, 0 bytes, Stack size 32 bytes, d2f.o(x$fpl$d2f))

[Stack]

- Max Depth = 32
- Call Chain = __aeabi_d2f

[Called By]

- >> encoderRead

_d2f (Thumb, 98 bytes, Stack size 32 bytes, d2f.o(x$fpl$d2f), UNUSED)

[Calls]

- >> __fpl_fretinf
- >> __fpl_dnaninf

__aeabi_dmul (Thumb, 0 bytes, Stack size 32 bytes, dmul.o(x$fpl$dmul))

[Stack]

- Max Depth = 32
- Call Chain = __aeabi_dmul

[Called By]

- >> encoderRead

_dmul (Thumb, 332 bytes, Stack size 32 bytes, dmul.o(x$fpl$dmul), UNUSED)

[Calls]

- >> __fpl_dretinf
- >> __fpl_dnaninf

__fpl_dnaninf (Thumb, 156 bytes, Stack size 16 bytes, dnaninf.o(x$fpl$dnaninf), UNUSED)

[Called By]

- >> _dmul
- >> _d2f

__fpl_dretinf (Thumb, 12 bytes, Stack size 0 bytes, dretinf.o(x$fpl$dretinf), UNUSED)

[Called By]

- >> _f2d
- >> _dmul

__aeabi_f2d (Thumb, 0 bytes, Stack size 16 bytes, f2d.o(x$fpl$f2d))

[Stack]

- Max Depth = 16
- Call Chain = __aeabi_f2d

[Called By]

- >> encoderRead

_f2d (Thumb, 86 bytes, Stack size 16 bytes, f2d.o(x$fpl$f2d), UNUSED)

[Calls]

- >> __fpl_fnaninf
- >> __fpl_dretinf

__aeabi_fadd (Thumb, 0 bytes, Stack size 16 bytes, faddsub_clz.o(x$fpl$fadd))

[Stack]

- Max Depth = 16
- Call Chain = __aeabi_fadd

[Called By]

- >> encoderRead
- >> TIM4_IRQHandler

_fadd (Thumb, 196 bytes, Stack size 16 bytes, faddsub_clz.o(x$fpl$fadd), UNUSED)

[Calls]

- >> __fpl_fretinf
- >> __fpl_fnaninf
- >> _fsub1

__aeabi_f2iz (Thumb, 0 bytes, Stack size 16 bytes, ffix.o(x$fpl$ffix))

[Stack]

- Max Depth = 16
- Call Chain = __aeabi_f2iz

[Called By]

- >> TIM4_IRQHandler

_ffix (Thumb, 54 bytes, Stack size 16 bytes, ffix.o(x$fpl$ffix), UNUSED)

[Calls]

- >> __fpl_fnaninf

__aeabi_i2f (Thumb, 0 bytes, Stack size 0 bytes, fflt_clz.o(x$fpl$fflt))

[Called By]

- >> encoderRead
- >> TIM4_IRQHandler

_fflt (Thumb, 48 bytes, Stack size 0 bytes, fflt_clz.o(x$fpl$fflt), UNUSED)

__aeabi_fmul (Thumb, 0 bytes, Stack size 16 bytes, fmul.o(x$fpl$fmul))

[Stack]

- Max Depth = 16
- Call Chain = __aeabi_fmul

[Called By]

- >> encoderRead
- >> TIM4_IRQHandler

_fmul (Thumb, 258 bytes, Stack size 16 bytes, fmul.o(x$fpl$fmul), UNUSED)

[Calls]

- >> __fpl_fretinf
- >> __fpl_fnaninf

__fpl_fnaninf (Thumb, 140 bytes, Stack size 8 bytes, fnaninf.o(x$fpl$fnaninf), UNUSED)

[Called By]

- >> _fmul
- >> _ffix
- >> _fsub
- >> _fadd
- >> _f2d

__fpl_fretinf (Thumb, 10 bytes, Stack size 0 bytes, fretinf.o(x$fpl$fretinf), UNUSED)

[Called By]

- >> _fmul
- >> _fadd
- >> _d2f

__aeabi_fsub (Thumb, 0 bytes, Stack size 16 bytes, faddsub_clz.o(x$fpl$fsub), UNUSED)

_fsub (Thumb, 234 bytes, Stack size 16 bytes, faddsub_clz.o(x$fpl$fsub), UNUSED)

[Calls]

- >> __fpl_fnaninf
- >> _fadd1

### Local Symbols

SetSysClock (Thumb, 8 bytes, Stack size 8 bytes, system_stm32f10x.o(i.SetSysClock))

[Stack]

- Max Depth = 20
- Call Chain = SetSysClock ⇒ SetSysClockTo72

[Calls]

- >> SetSysClockTo72

[Called By]

- >> SystemInit

SetSysClockTo72 (Thumb, 214 bytes, Stack size 12 bytes, system_stm32f10x.o(i.SetSysClockTo72))

[Stack]

- Max Depth = 12
- Call Chain = SetSysClockTo72

[Called By]

- >> SetSysClock

_fadd1 (Thumb, 0 bytes, Stack size unknown bytes, faddsub_clz.o(x$fpl$fadd), UNUSED)

[Called By]

- >> _fsub

_fsub1 (Thumb, 0 bytes, Stack size unknown bytes, faddsub_clz.o(x$fpl$fsub), UNUSED)

[Called By]

- >> _fadd

### Undefined Global Symbols

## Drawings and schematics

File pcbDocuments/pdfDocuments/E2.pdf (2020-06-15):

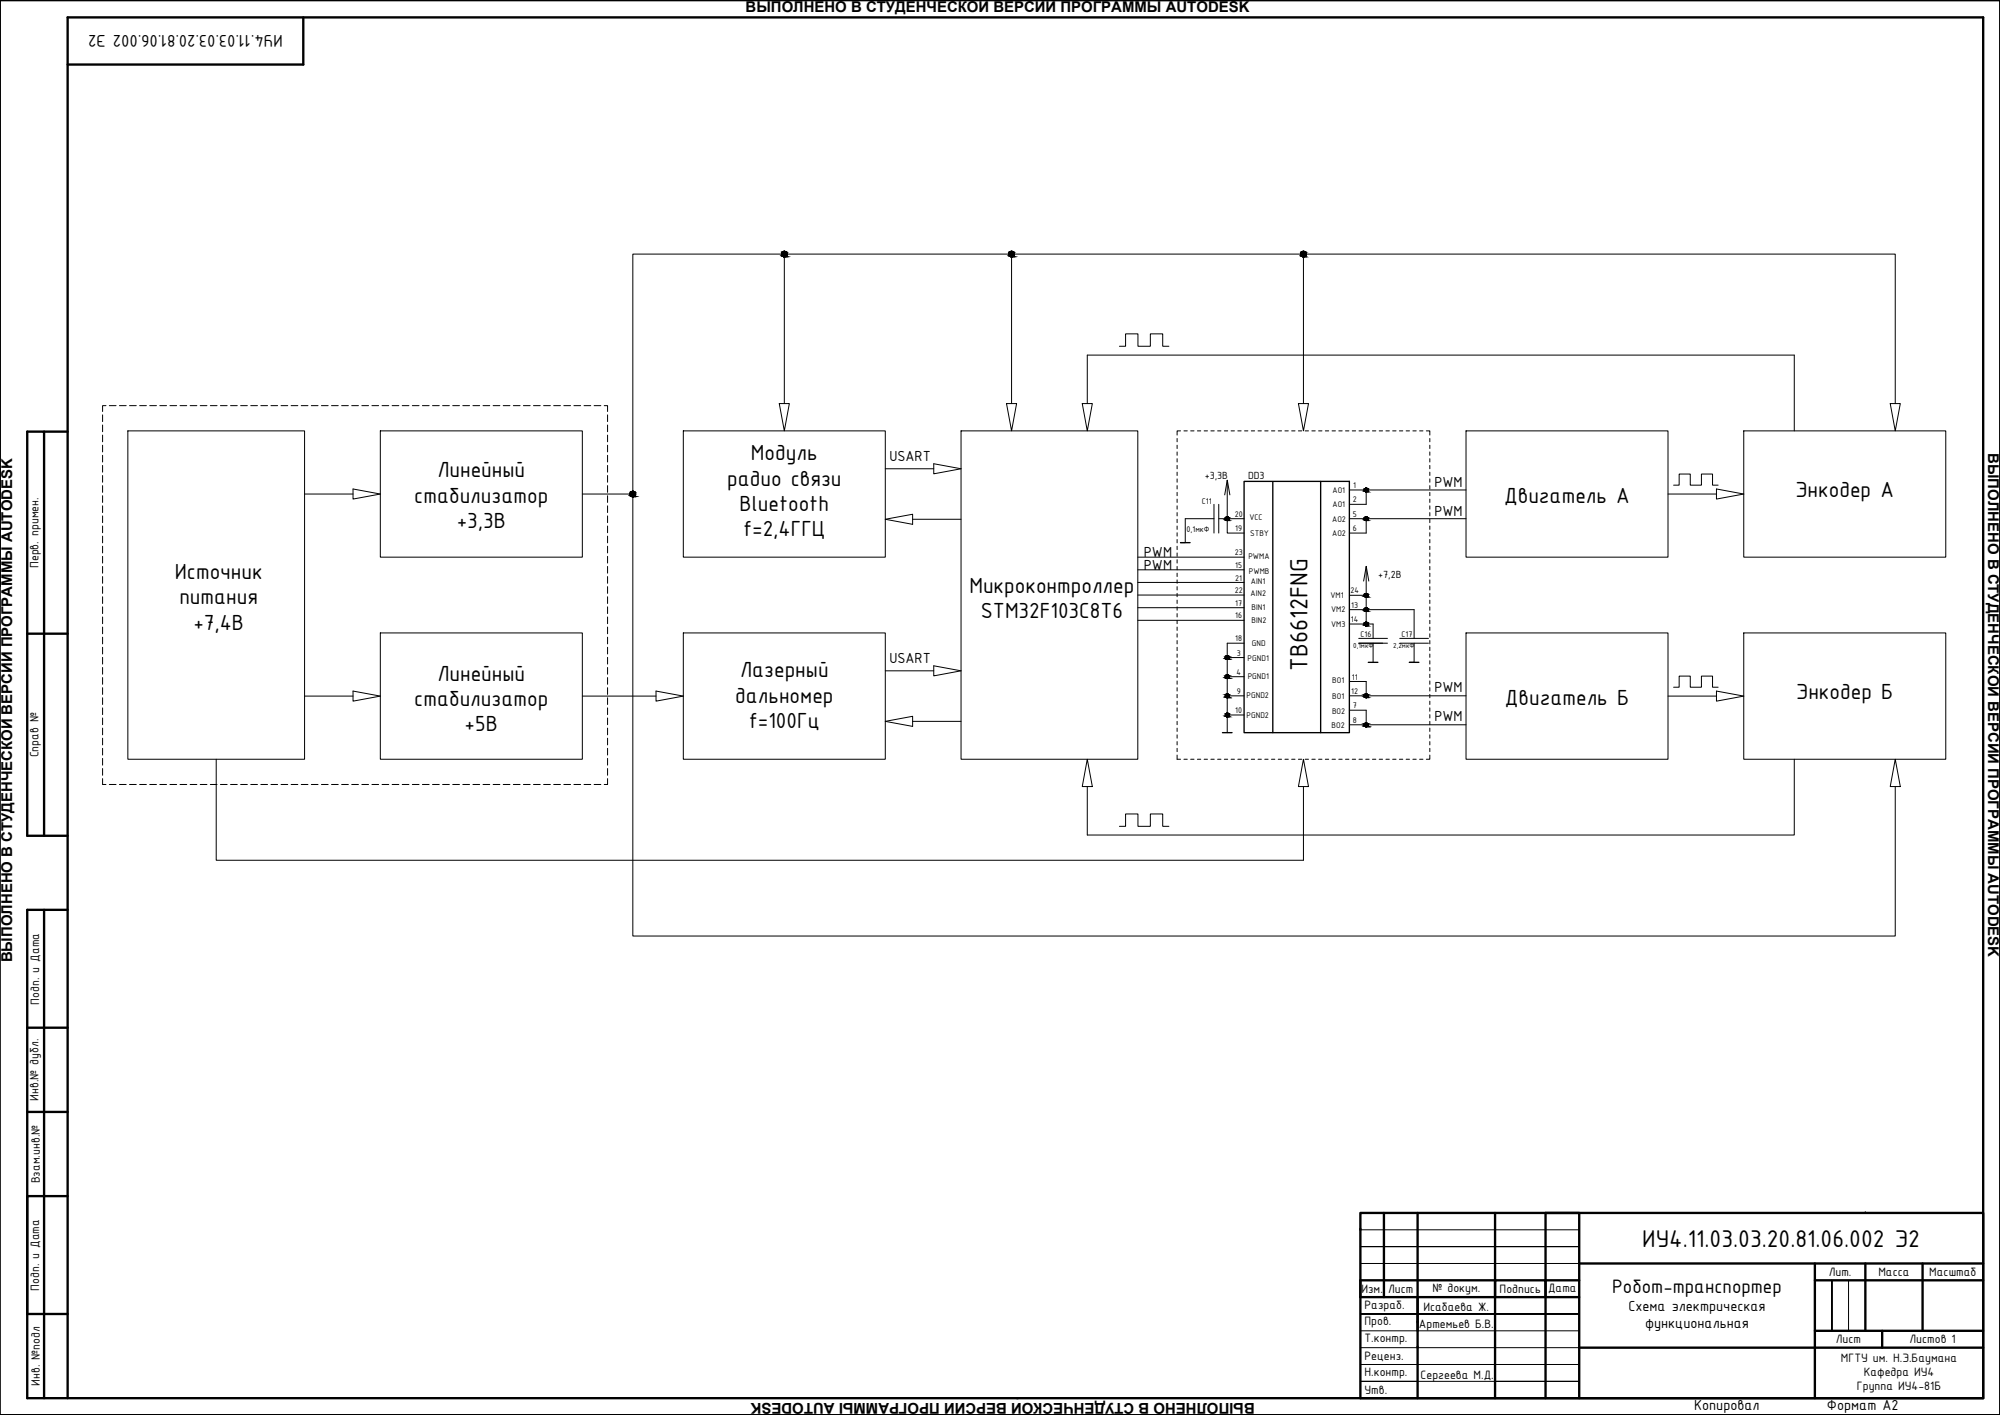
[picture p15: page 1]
Источник питания +7,4В; Линейный стабилизатор +3,3В Линейный стабилизатор +5В; Модуль радио связи Bluetooth f=2,4ГГЦ Лазерный дальномер f=100Гц; Микроконтроллер STM32F103C8T6; Двигатель A; Энкодер A Двигатель Б; Энкодер Б USART USART; VCC; VM1 VM2 VM3 BO1 BO1 BO2 BO2 PWMA PWMB AIN1 AIN2 BIN2 STBY PGND1 PGND1 PGND2 PGND2

ВЫПОЛНЕНО В СТУДЕНЧЕСКОЙ ВЕРСИИ ПРОГРАММЫ AUTODESK

Инв. №подл Подп. и Дата Взам.инв.№ Инв.№ дубл. Подп. и Дата Справ № Перв. примен. 2Э 4.11.03.03.20.81.06.002 ИУ Исабаева Ж. Сергеева М.Д. PWM PWM PWM C16 DD3 1521 22171618349101920 2465211314111278 Артемьев Б.В. PWM AO2 AO1 AO1 BIN1

TB6612FNG AO2 +7,2B GND +3,3B C17 0,1мкФ 2,2мкФ C11 0,1мкФ PWM PWM Разраб. Пров. Изм. Лист № докум. Подпись Дата Лит. Масса Масштаб Т.контр. Лист Листов 1 Реценз. Н.контр. Утв. ИУ4.11.03.03.20.81.06.002 Э2 МГТУ им. Н.Э.Баумана Кафедра ИУ4 Группа ИУ4-81Б Робот-транспортер Схема электрическая функциональная Копировал Формат A2

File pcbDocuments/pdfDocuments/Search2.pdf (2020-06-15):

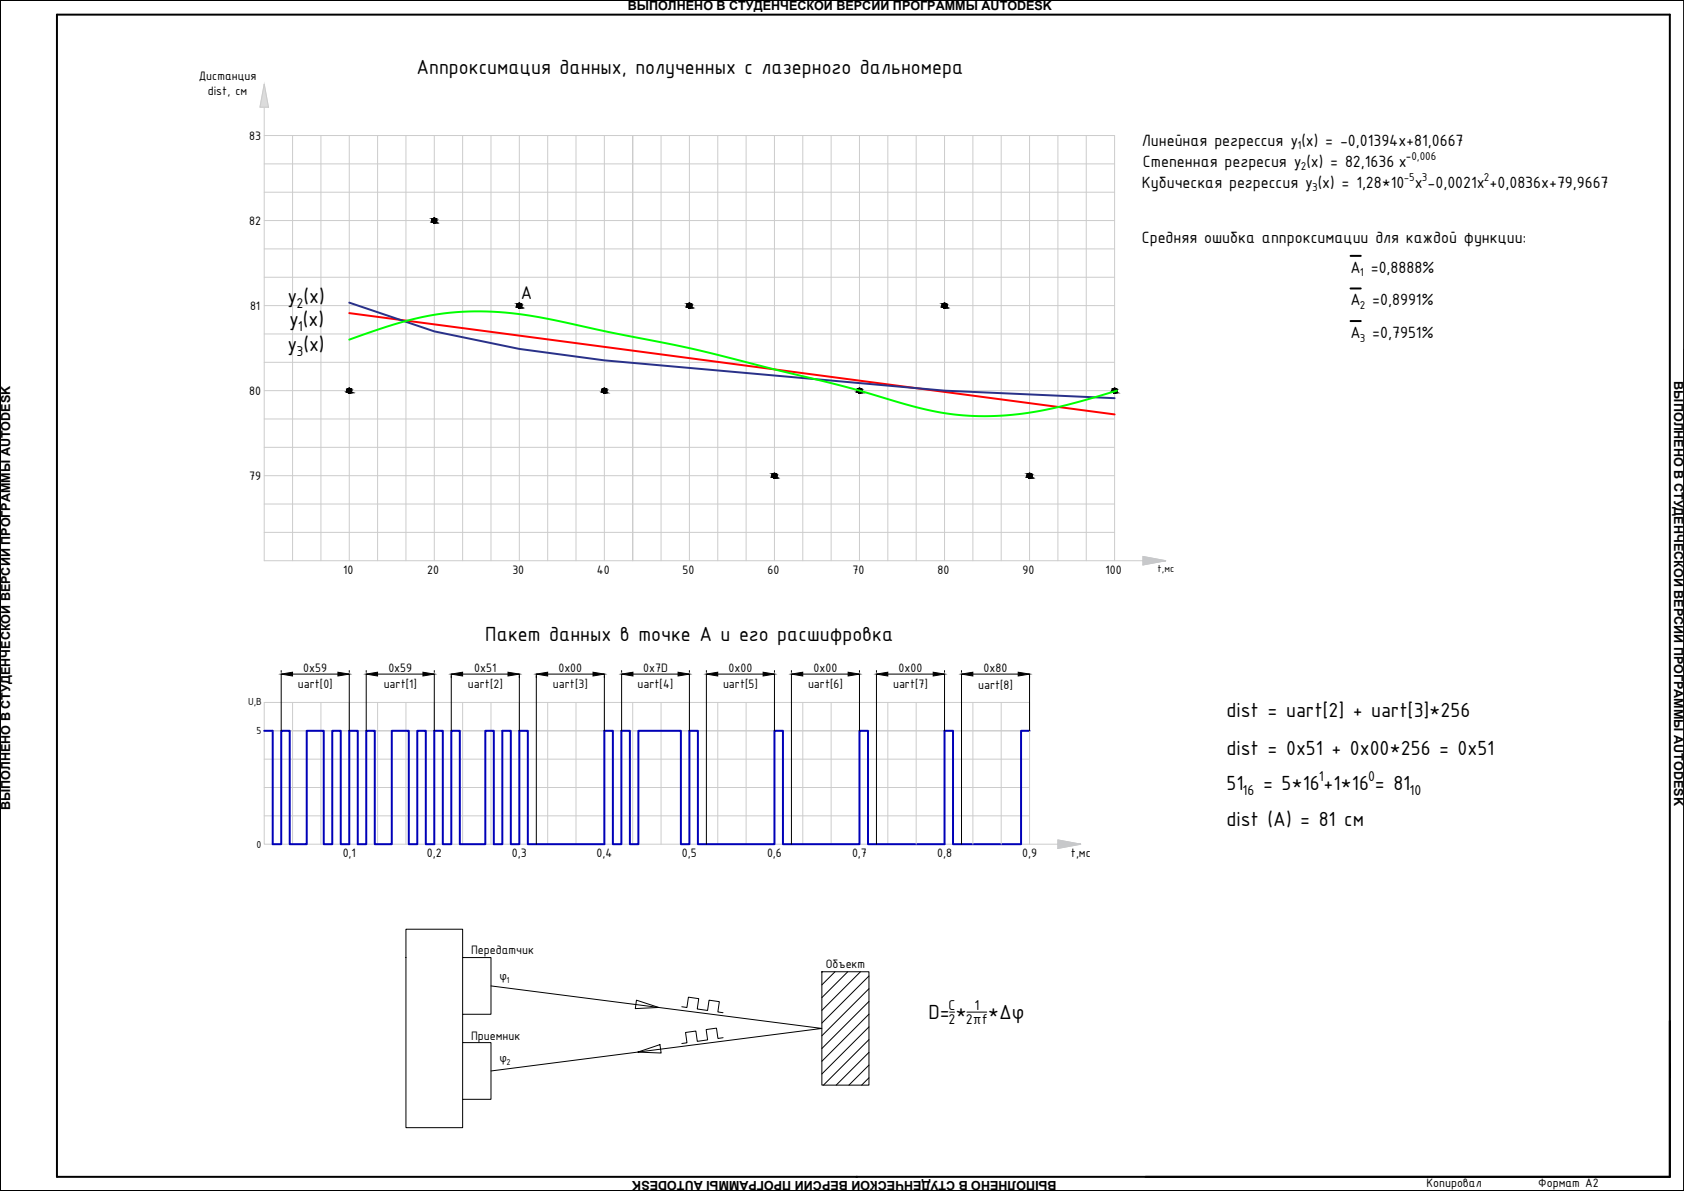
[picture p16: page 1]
Копировал; Формат A2 Аппроксимация данных, полученных с лазерного; дальномера 10; 20 Дистанция dist, см; 0x00 uart[2]; uart[3]; dist = uart[2] + uart[3]*256 dist = 0x51 + 0x00*256 = 0x51 5116 = 5*161+1*160= 8110 dist (A) = 81 см t,мс Пакет данных в точке A и его расшифровка 30; 0x80 uart[0]; uart[1]; uart[4]; uart[5]; uart[6]; uart[7]; uart[8] y2(x) y3(x)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

ВЫПОЛНЕНО В СТУДЕНЧЕСКОЙ ВЕРСИИ ПРОГРАММЫ AUTODESK

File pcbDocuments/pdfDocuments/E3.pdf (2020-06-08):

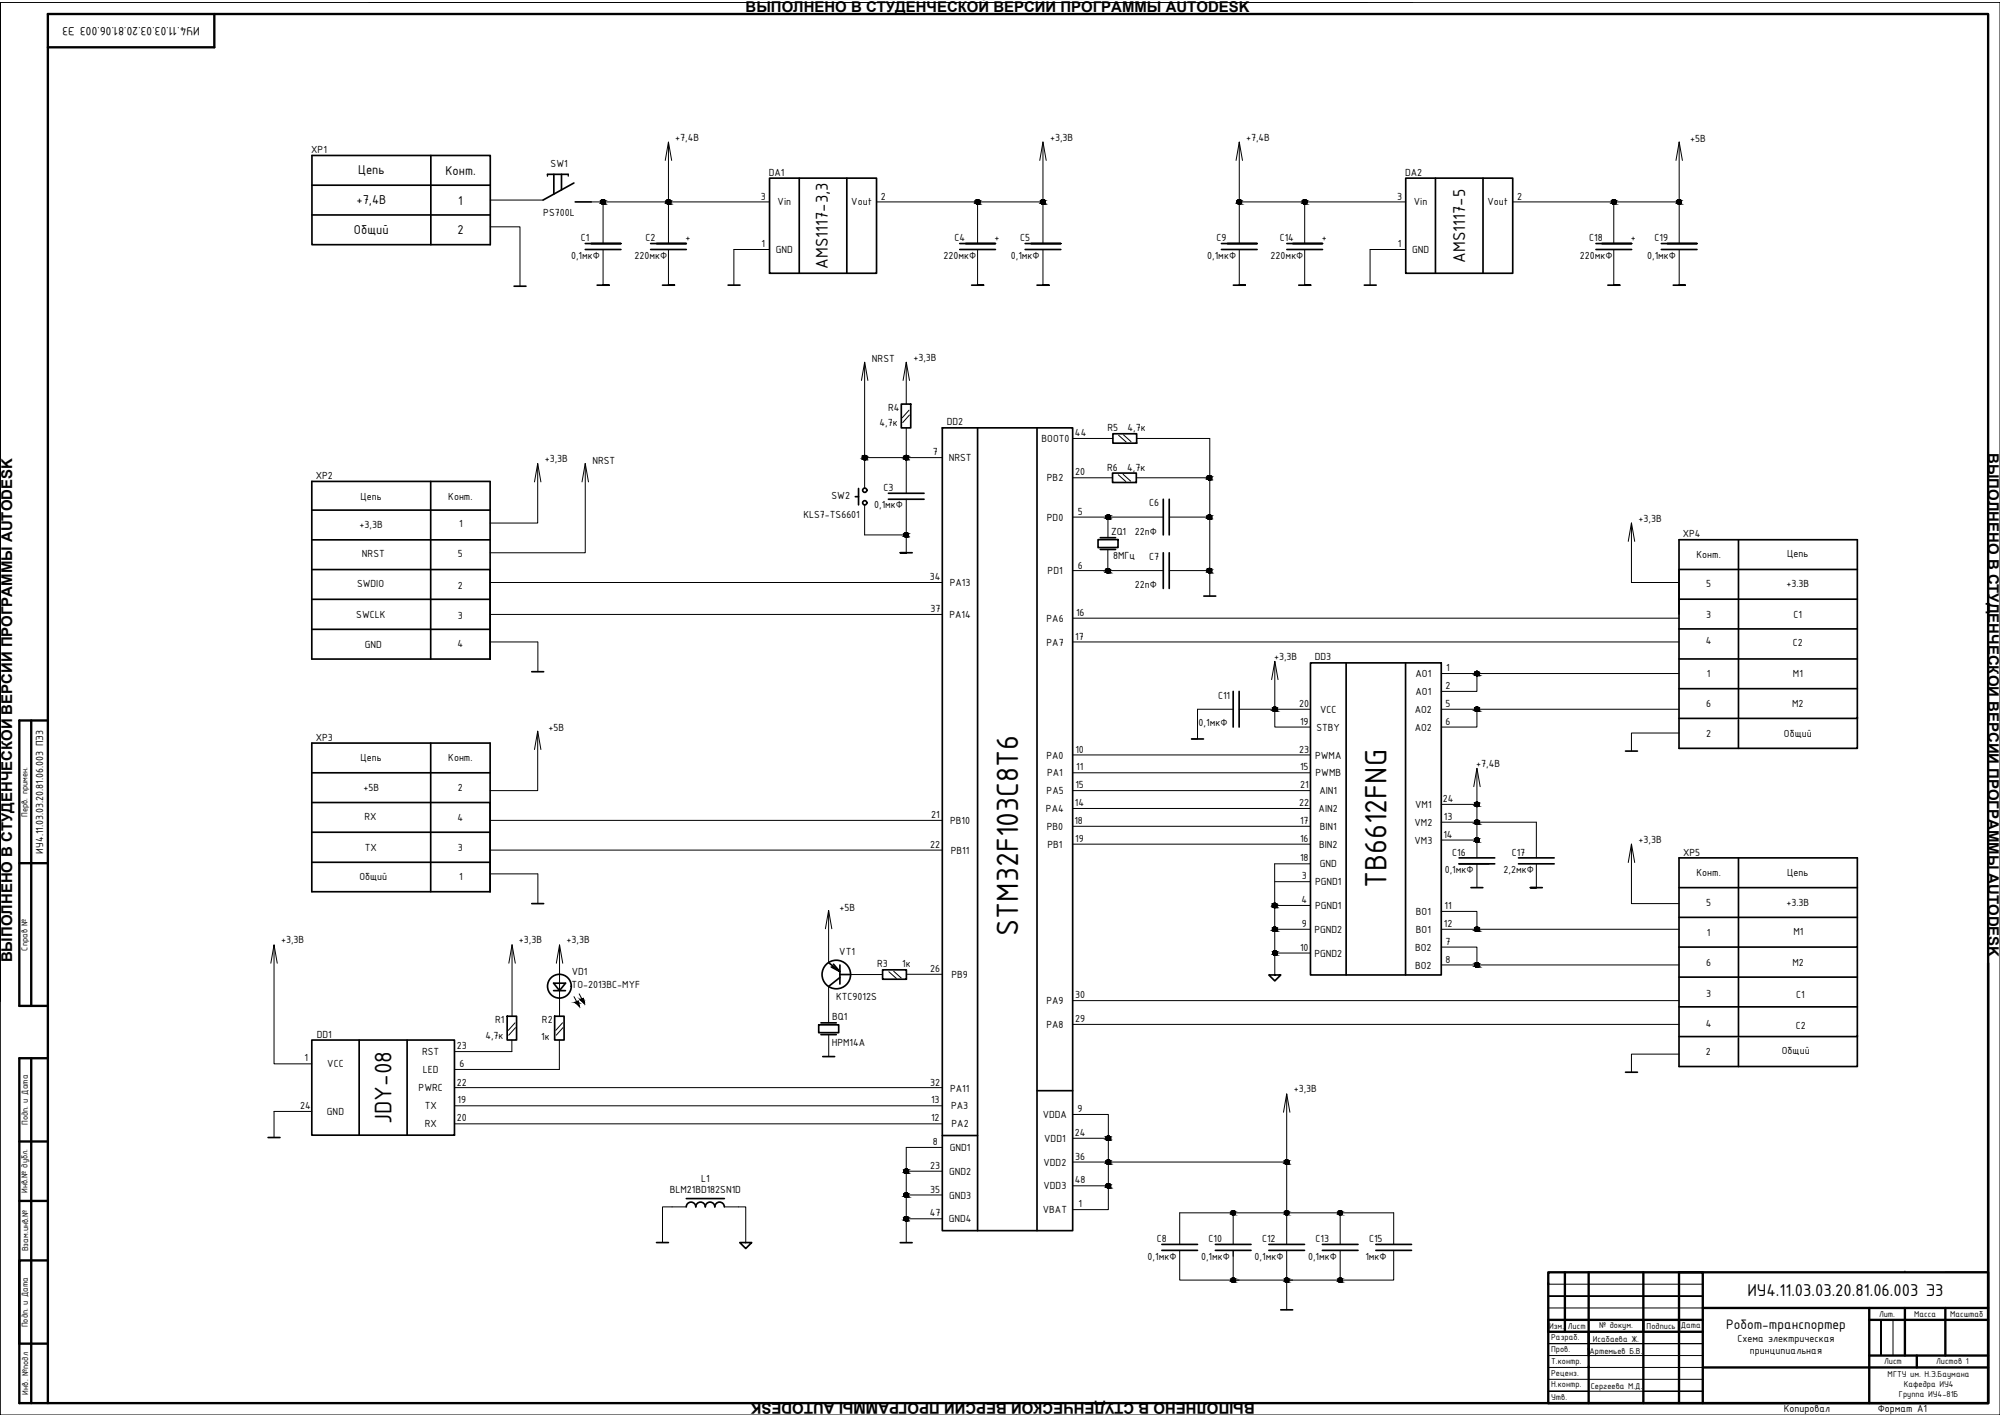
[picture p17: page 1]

ВЫПОЛНЕНО В СТУДЕНЧЕСКОЙ ВЕРСИИ ПРОГРАММЫ AUTODESK

AMS1117-5 GND Vin Vout VD1 +3,3B Цепь 32 Конт. SWDIO SWCLK GND 41 NRST 5 20 +3,3B BQ1 L1 VT1 KTC9012S TO-2013BC-MYF BLM21BD182SN1D BO2 BO1 BO1 VM3 VM2 VM1 AO2 AO1 AO1 PB2 PD0 PD1 PA6 PA7 PA1 PB1 PB0 PA4 PA5 1110 VDDA VDD1 VDD2 VDD3 VBAT 92436481 233547121332 PA2 PA3 PA11 26 PB9 22 PB11 21 PB10 37 PA14 34 PA13 7 NRST 19231521 2217161834910 712111413246521 236221920 LED PWRC TXRX +3,3B R2 1к R4 4,7к R6 4,7к R3 1к +5B +3,3B NRST +3,3B NRST +7,4В +3,3B +7,4B +5В +3,3B +3,3B +3,3B +3,3B 3 2 1 DA1 GND Vin Vout 3 2 1 XP2 XP3 DD1 DD2 XP5 XP4 DD3 C1 0,1мкФ C2 220мкФ C4 220мкФ C5 0,1мкФ C9 0,1мкФ C19 0,1мкФ C14 220мкФ C18 220мкФ + + + +5B C8 0,1мкФ C10 0,1мкФ C12 0,1мкФ C13 0,1мкФ C15 1мкФ C16 0,1мкФ C17 2,2мкФ C6 22пФ Исабаева Ж. Сергеева М.Д. ZQ1 8МГц HPM14A PS700L KLS7-TS6601 C7 22пФ C11 0,1мкФ Артемьев Б.В.

JDY-08 +5B Цепь 42 Конт. RXTX 3 Общий 1 + DA2 C3 0,1мкФ SW1 SW2 R5 4,7к R1 4,7к +3,3B

AMS1117-3,3 8 GND1 GND2 GND3 GND4 2930 PA8 PA9 19181415 PA0 1716544 BOOT0 +3.3B C1 Цепь 15 Конт. M1 M2 4 C2 362 Общий AO2 +7,4B GND 4 STM32F103C8T6 6 RST VCC GND 124

ИУ4.11.03.03.20.81.06.003 ПЭ3 Копировал Формат A1 +3.3B C1 Цепь 35 Конт. M1 M2C2 612 Общий 20 8 VCC BO2 PWMA PWMB AIN1 AIN2 BIN1 BIN2 STBY PGND1 PGND1 PGND2 PGND2

Инв. №подл Подп. и Дата Взам.инв.№ Инв.№ дубл. Подп. и Дата Справ № Перв. примен. Разраб. Пров. Изм. Лист № докум. Подпись Дата Лит. Масса Масштаб Т.контр. Лист Листов 1 Реценз. Н.контр. Утв. ИУ4.11.03.03.20.81.06.003 Э3 МГТУ им. Н.Э.Баумана Кафедра ИУ4 Группа ИУ4-81Б Робот-транспортер Схема электрическая принципиальная

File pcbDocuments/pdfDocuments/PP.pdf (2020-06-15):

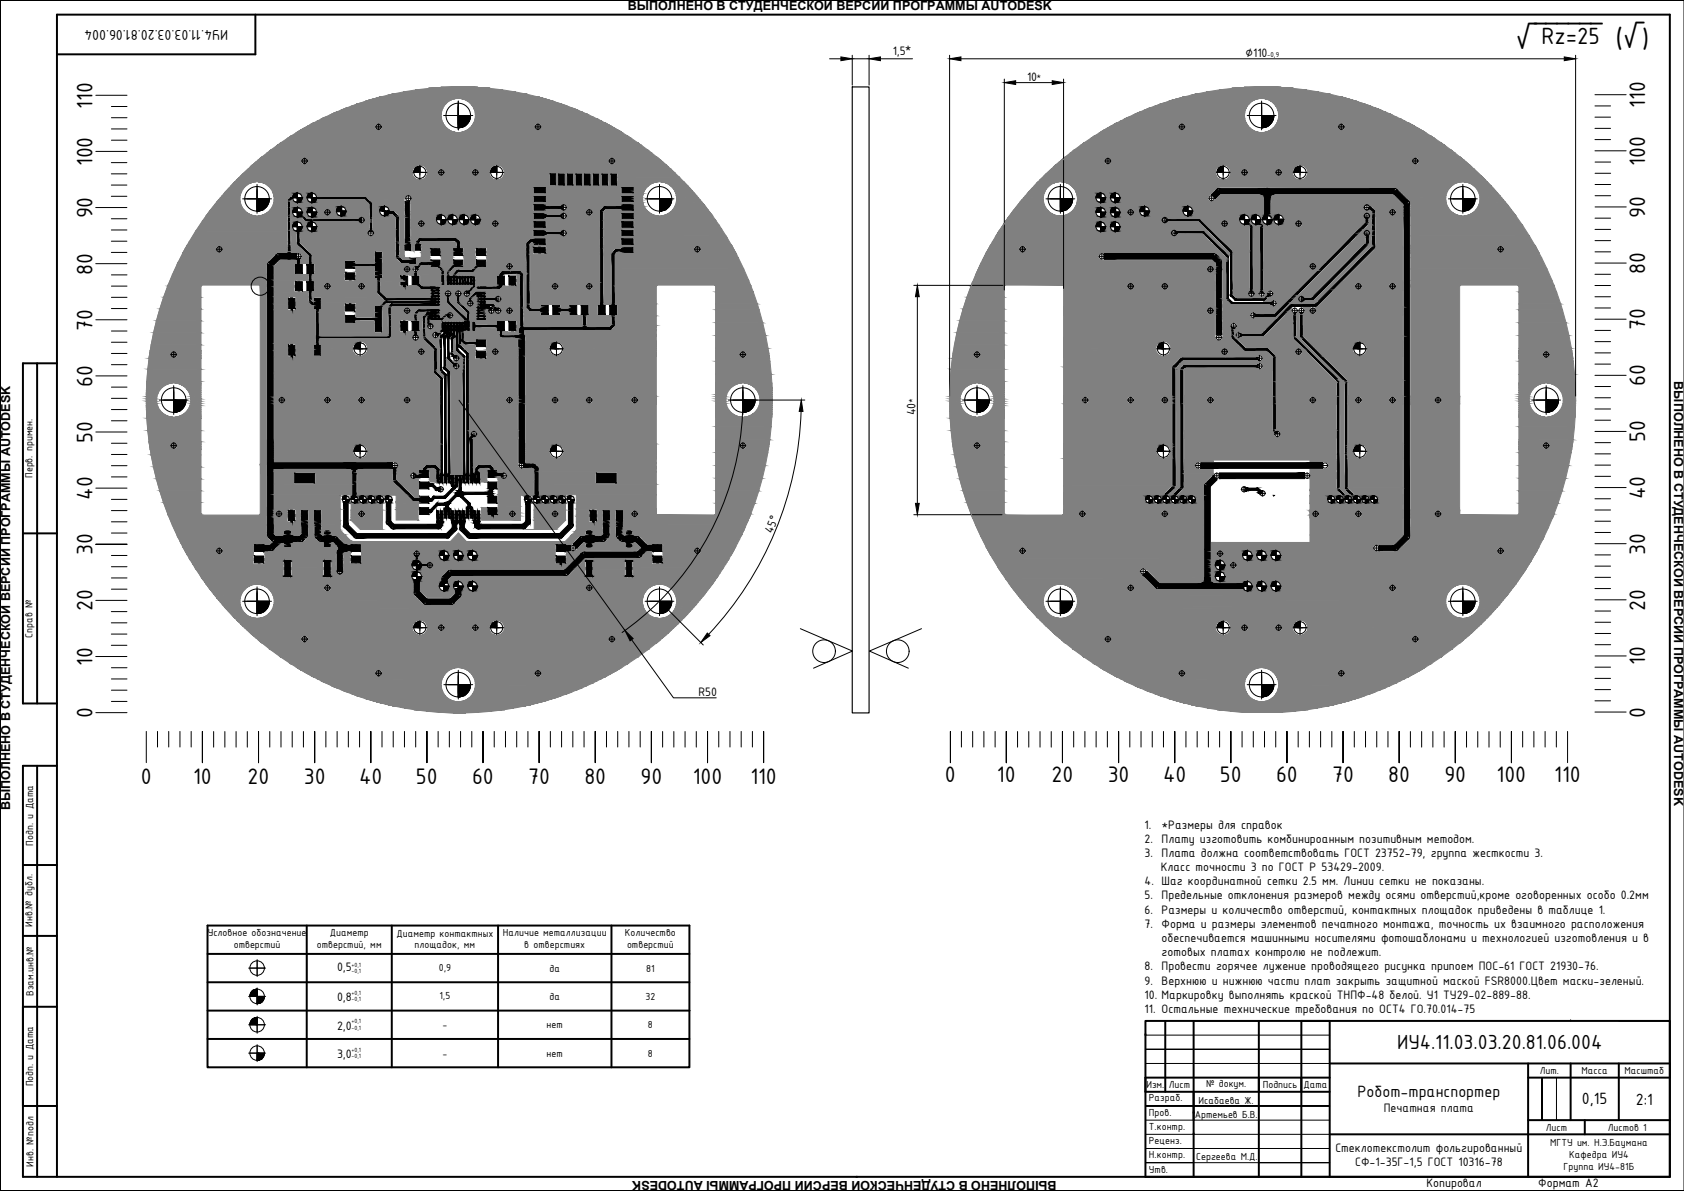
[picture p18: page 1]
1. *Размеры для справок 2. Плату изготовить комбинироанным позитивным методом. 3. Плата должна соответствовать ГОСТ 23752-79, группа жесткости 3. Класс точности 3 по ГОСТ Р 53429-2009. 4. Шаг координатной сетки 2.5 мм. Линии сетки не показаны. 5. Предельные отклонения размеров между осями отверстий,кроме оговоренных особо 0.2мм 6. Размеры и количество отверстий, контактных площадок приведены в таблице 1. 7. Форма и размеры элементов печатного монтажа, точность их взаимного расположения обеспеч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

ВЫПОЛНЕНО В СТУДЕНЧЕСКОЙ ВЕРСИИ ПРОГРАММЫ AUTODESK

Инв. №подл Подп. и Дата Взам.инв.№ Инв.№ дубл. Подп. и Дата Справ № Перв. примен. 4.11.03.03.20.81.06.004 ИУ

40 50 30 10 0 20 100 110 90 70 60 80 0 10 20 30 40 50 60 70 80 90 100 110 Условное обозначение отверстий Диаметр отверстий, мм Диаметр контактных площадок, мм Наличие металлизации в отверстиях Количество отверстий 0,5+0,1 -0,1 0,8+0,1 -0,1 2,0+0,1 -0,1 3,0+0,1 -0,1 0,9 1,5-- дада нет нет 81 3288 2:1 Стеклотекстолит фольгированный СФ-1-35Г-1,5 ГОСТ 10316-78 0,15 Сергеева М.Д. Артемьев Б.В.

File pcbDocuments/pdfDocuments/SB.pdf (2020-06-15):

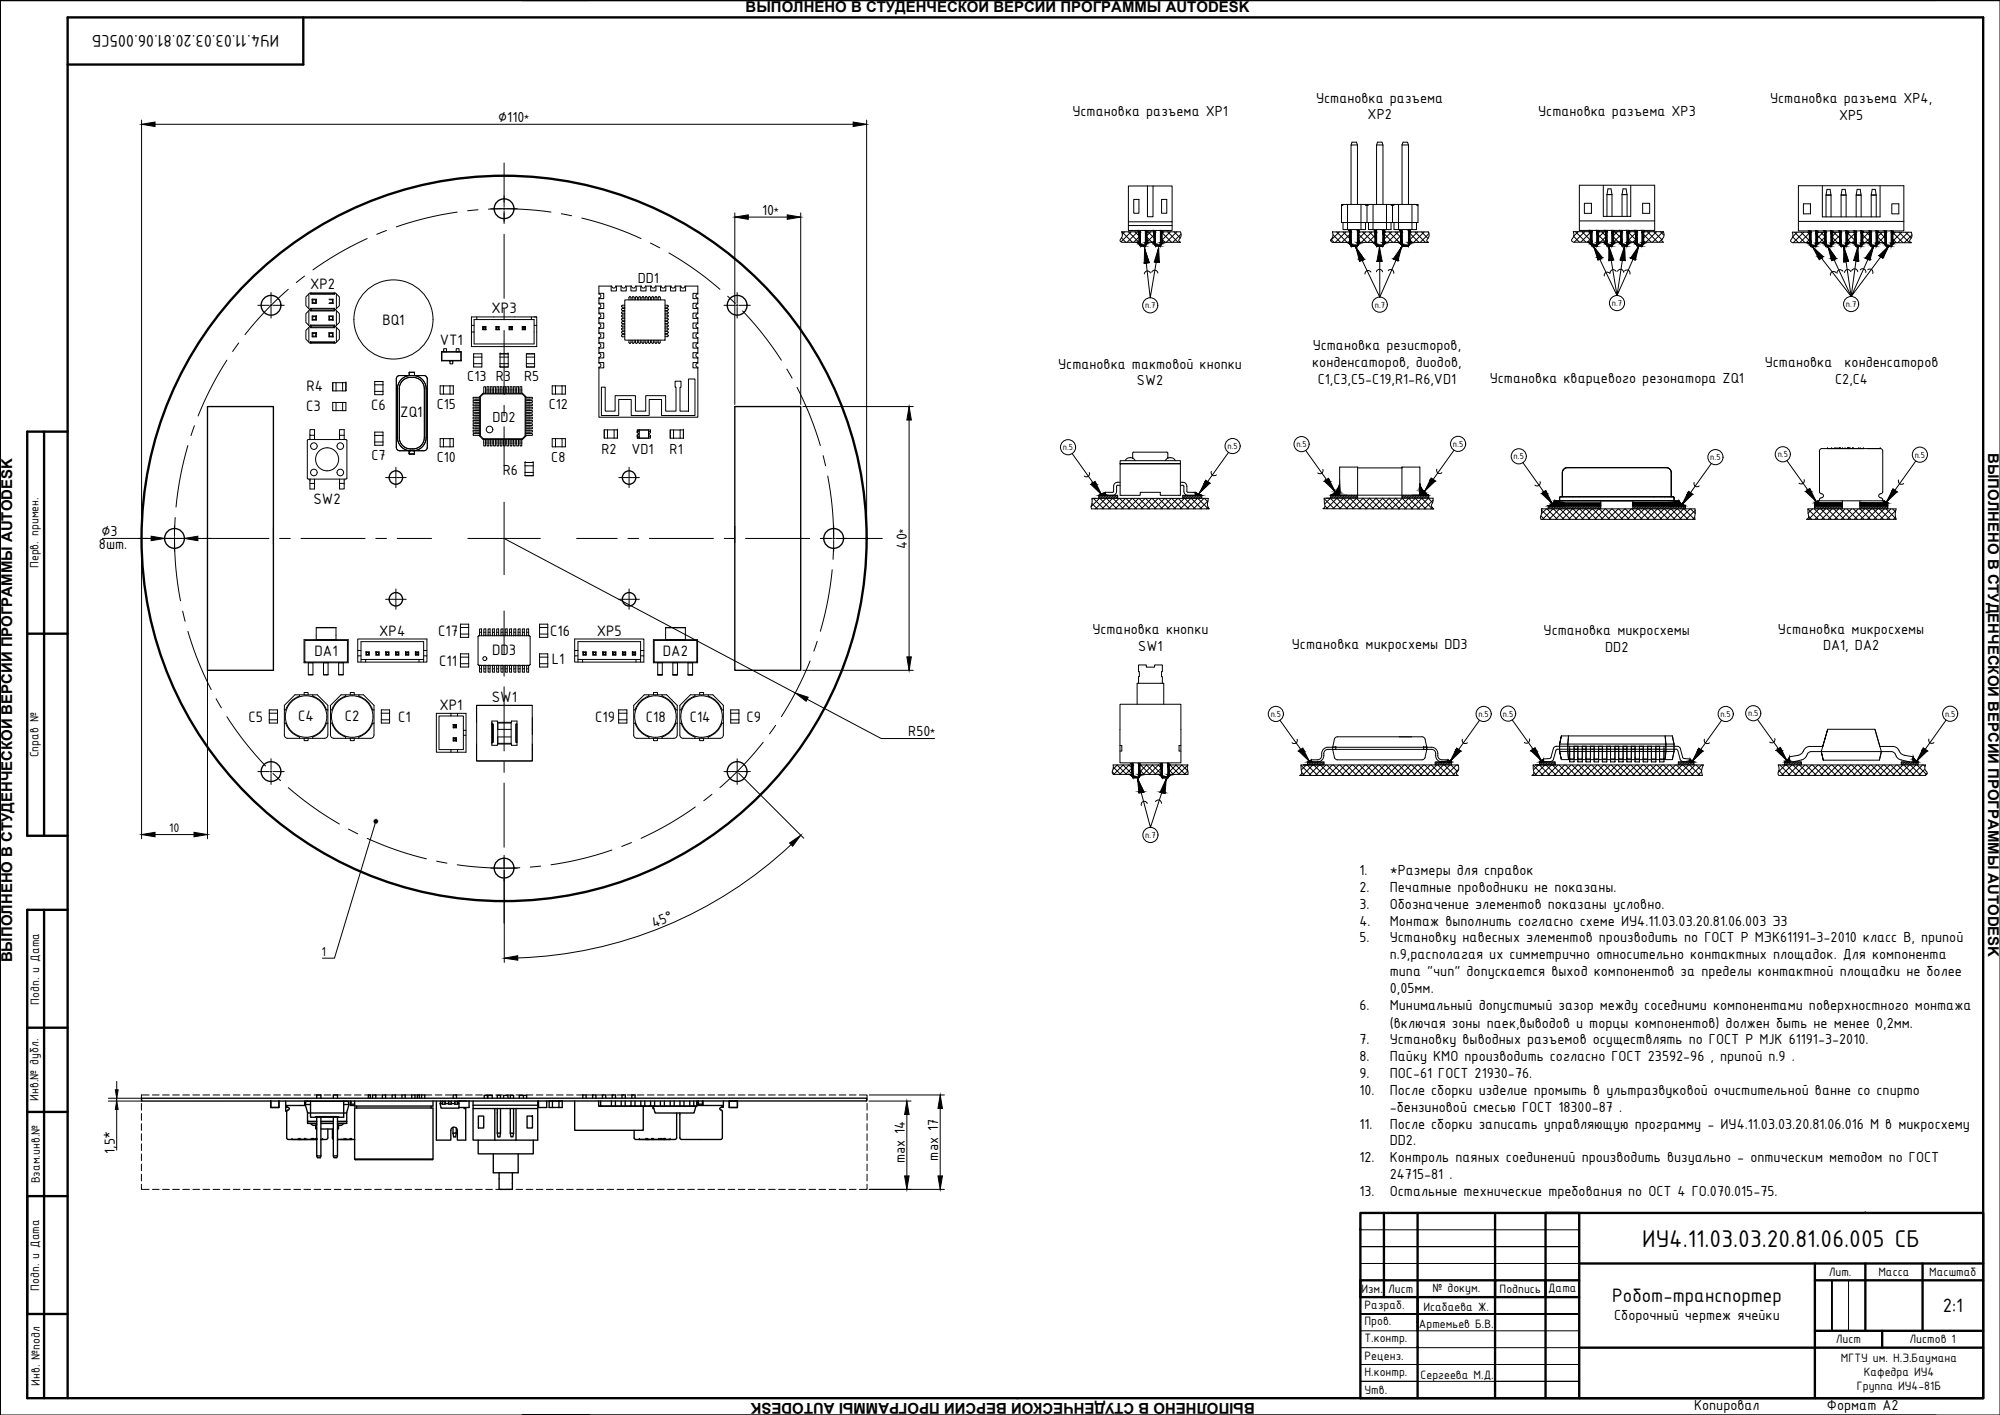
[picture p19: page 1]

ВЫПОЛНЕНО В СТУДЕНЧЕСКОЙ ВЕРСИИ ПРОГРАММЫ AUTODESK

Инв. №подл Подп. и Дата Взам.инв.№ Инв.№ дубл. Подп. и Дата Справ № Перв. примен. СБ 4.11.03.03.20.81.06.005 ИУ 2:1 Сергеева М.Д. C5 C4 C2 C1 C18 C14 XP1 SW1 DD3 C17 C11 C16 L1 XP5 DA1 DA2 XP4 DD1 R2 VD1 R1 BQ1ZQ1 DD2 XP3 XP2 R6 C15 SW2 C3R4 VT1 C13 R3 R5

40* 10* ∅3 8шт. R50* ∅110* 45° C19 C9 C12 C10 C8 C6C7 Установка разъема XP4, XP5 п.7 п.7 п.7 п.5 п.5 п.5 п.5 п.5 п.5 п.5 п.5 п.5 п.5 п.5 п.5 п.7 Установка разъема XP1 Установка разъема XP2 Установка микросхемы DD2 Установка кварцевого резонатора ZQ1 Установка микросхемы DD3 Установка микросхемы DA1, DA2 Установка резисторов, конденсаторов, диодов, С1,С3,С5-С19,R1-R6,VD1 Установка конденсаторов С2,С4 Установка кнопки SW1 п.5 п.5 Установка тактовой кнопки SW2 1. *Размеры для справок 2. Печатные проводники не показаны. 3. Обозначение элементов показаны условно. 4. Монтаж выполнить согласно схеме ИУ4.11.03.03.20.81.06.003 Э3 5. Установку навесных элементов производить по ГОСТ Р МЭК61191-3-2010 класс B, припой п.9,располагая их симметрично относительно контактных площадок. Для компонента типа "чип" допускается выход компонентов за пределы контактной площадки не более 0,05мм. 6. Минимальный допустимый зазор между соседними компонентами поверхностного монтажа (включая зоны паек,выводов и торцы компонентов) должен быть не менее 0,2мм. 7. Установку выводных разъемов осуществлять по ГОСТ Р MJK 61191-3-2010. 8. Пайку КМО производить согласно ГОСТ 23592-96 , припой п.9 . 9. ПОС-61 ГОСТ 21930-76. 10. После сборки изделие промыть в ультразвуковой очистительной ванне со спирто -бензиновой смесью ГОСТ 18300-87 . 11. После сборки записать управляющую программу - ИУ4.11.03.03.20.81.06.016 М в микросхему DD2. 12. Контроль паяных соединений производить визуально - оптическим методом по ГОСТ 24715-81 . 13. Остальные технические требования по ОСТ 4 ГО.070.015-75.

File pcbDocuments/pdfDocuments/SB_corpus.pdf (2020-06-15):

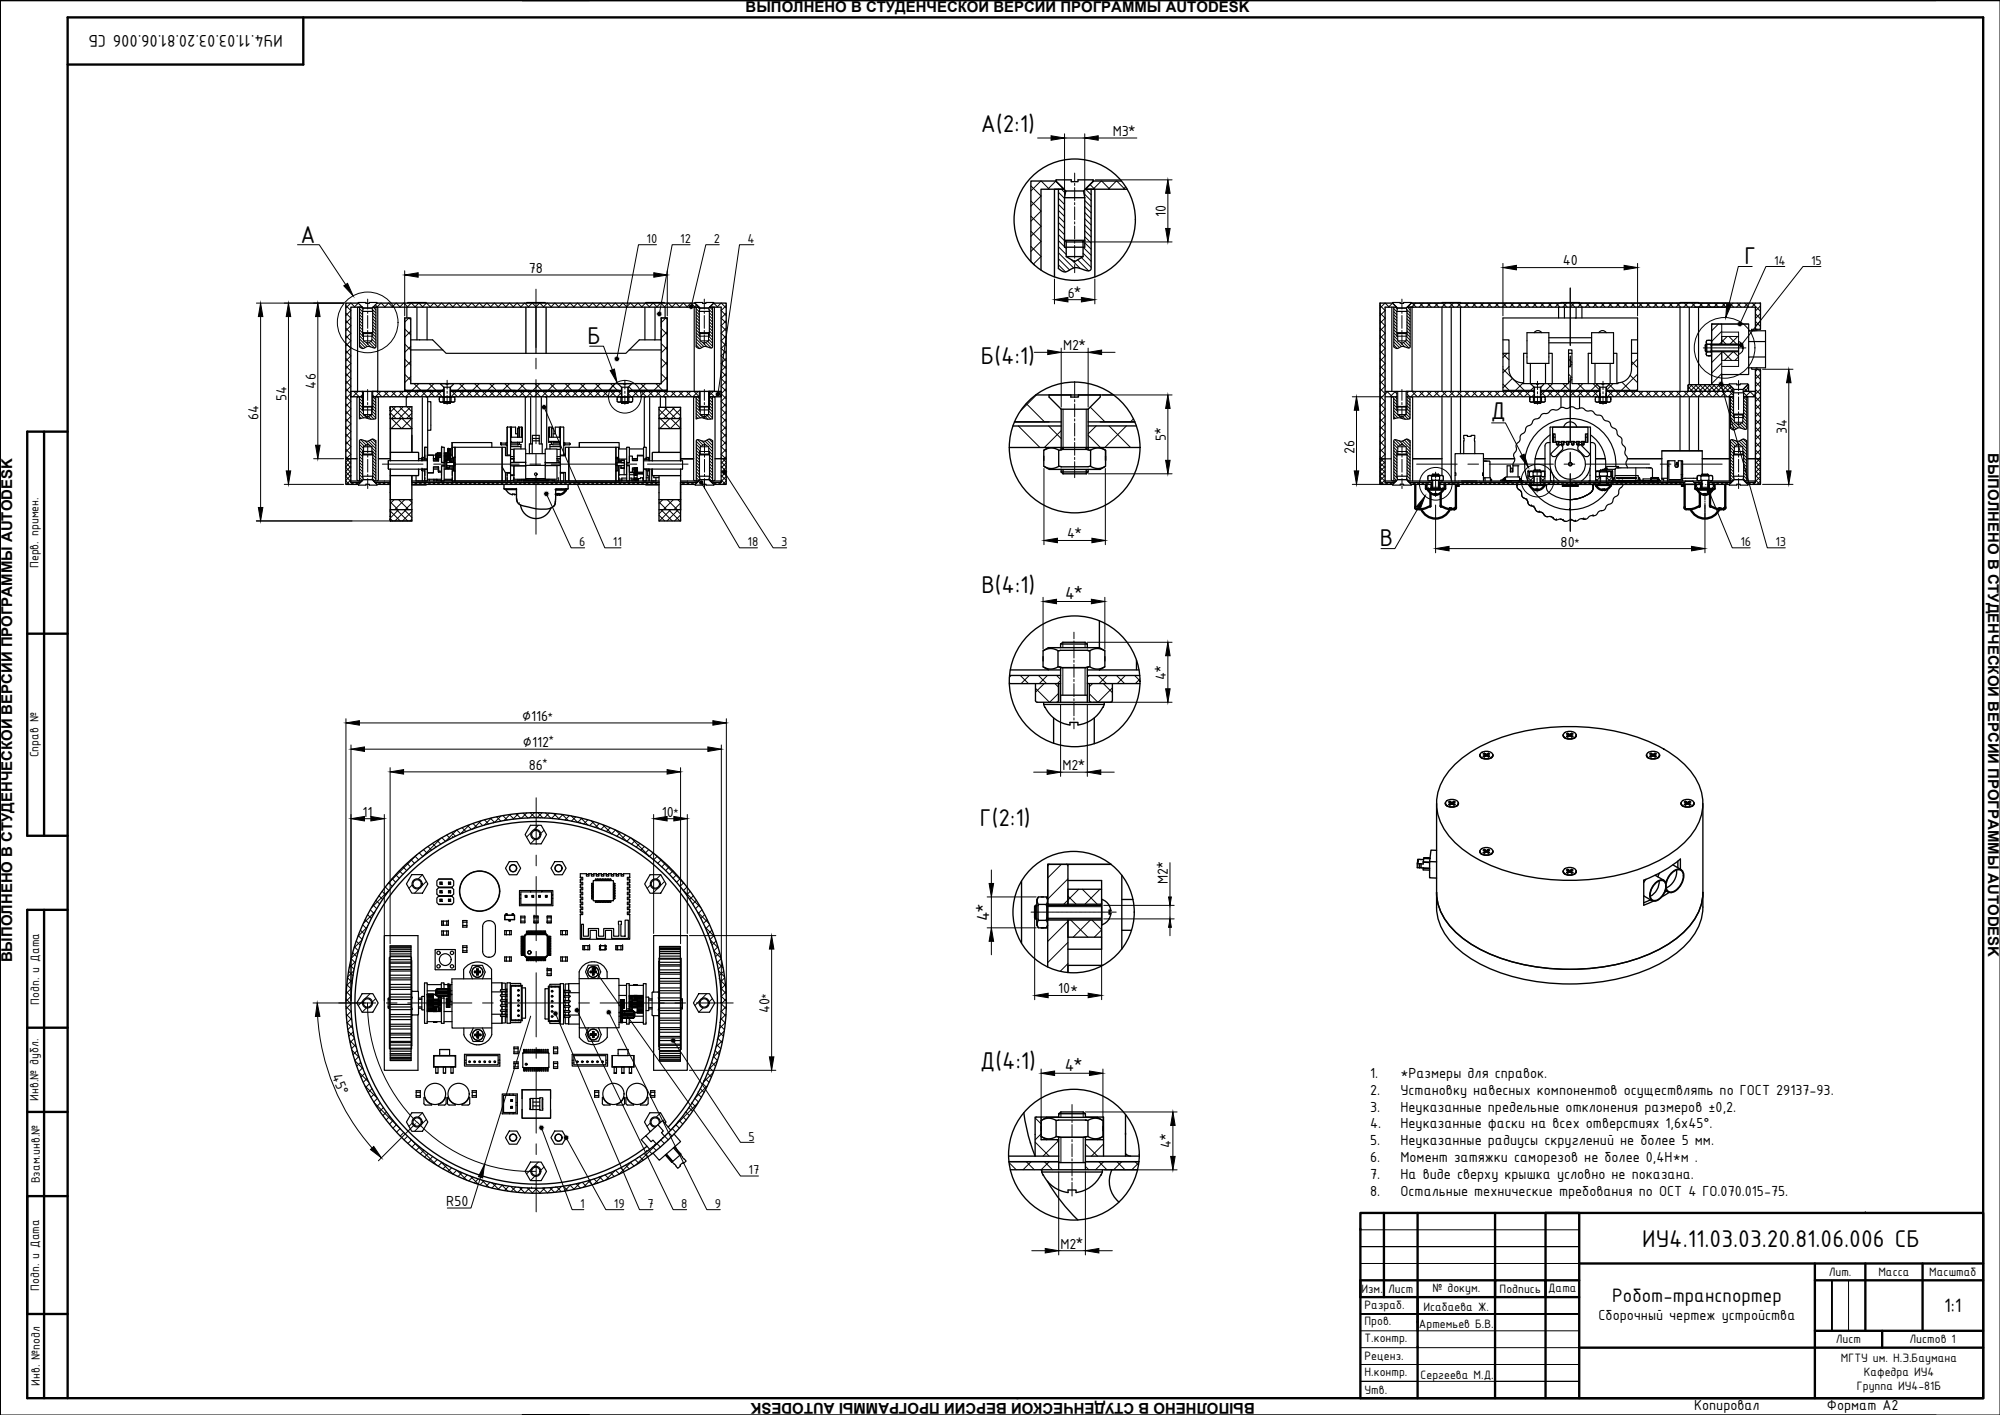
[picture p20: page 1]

ВЫПОЛНЕНО В СТУДЕНЧЕСКОЙ ВЕРСИИ ПРОГРАММЫ AUTODESK

Инв. №подл Подп. и Дата Взам.инв.№ Инв.№ дубл. Подп. и Дата Справ № Перв. примен. СБ 4.11.03.03.20.81.06.006 ИУ 1:1 Сергеева М.Д. ∅116* R50 ∅112* 86* 1 5 19 7 8 9 17 Г 10* 4* Г(2:1) A(2:1)

34 80* 2 3 4 6 10 11 12 14 18 В 16 13 M2* 4* В(4:1) 4* Разраб. Пров. Изм. Лист № докум. Подпись Дата Лит. Масса Масштаб Т.контр. Лист Листов 1 Реценз. Н.контр. Утв. ИУ4.11.03.03.20.81.06.006 СБ МГТУ им. Н.Э.Баумана Кафедра ИУ4 Группа ИУ4-81Б Робот-транспортер Сборочный чертеж устройства Исабаева Ж. Артемьев Б.В. Копировал Формат A2

40* 11 10* 1. *Размеры для справок. 2. Установку навесных компонентов осуществлять по ГОСТ 29137-93. 3. Неуказанные предельные отклонения размеров ±0,2. 4. Неуказанные фаски на всех отверстиях 1,6х45°. 5. Неуказанные радиусы скруглений не более 5 мм. 6. Момент затяжки саморезов не более 0,4Н*м . 7. На виде сверху крышка условно не показана. 8. Остальные технические требования по ОСТ 4 ГО.070.015-75.

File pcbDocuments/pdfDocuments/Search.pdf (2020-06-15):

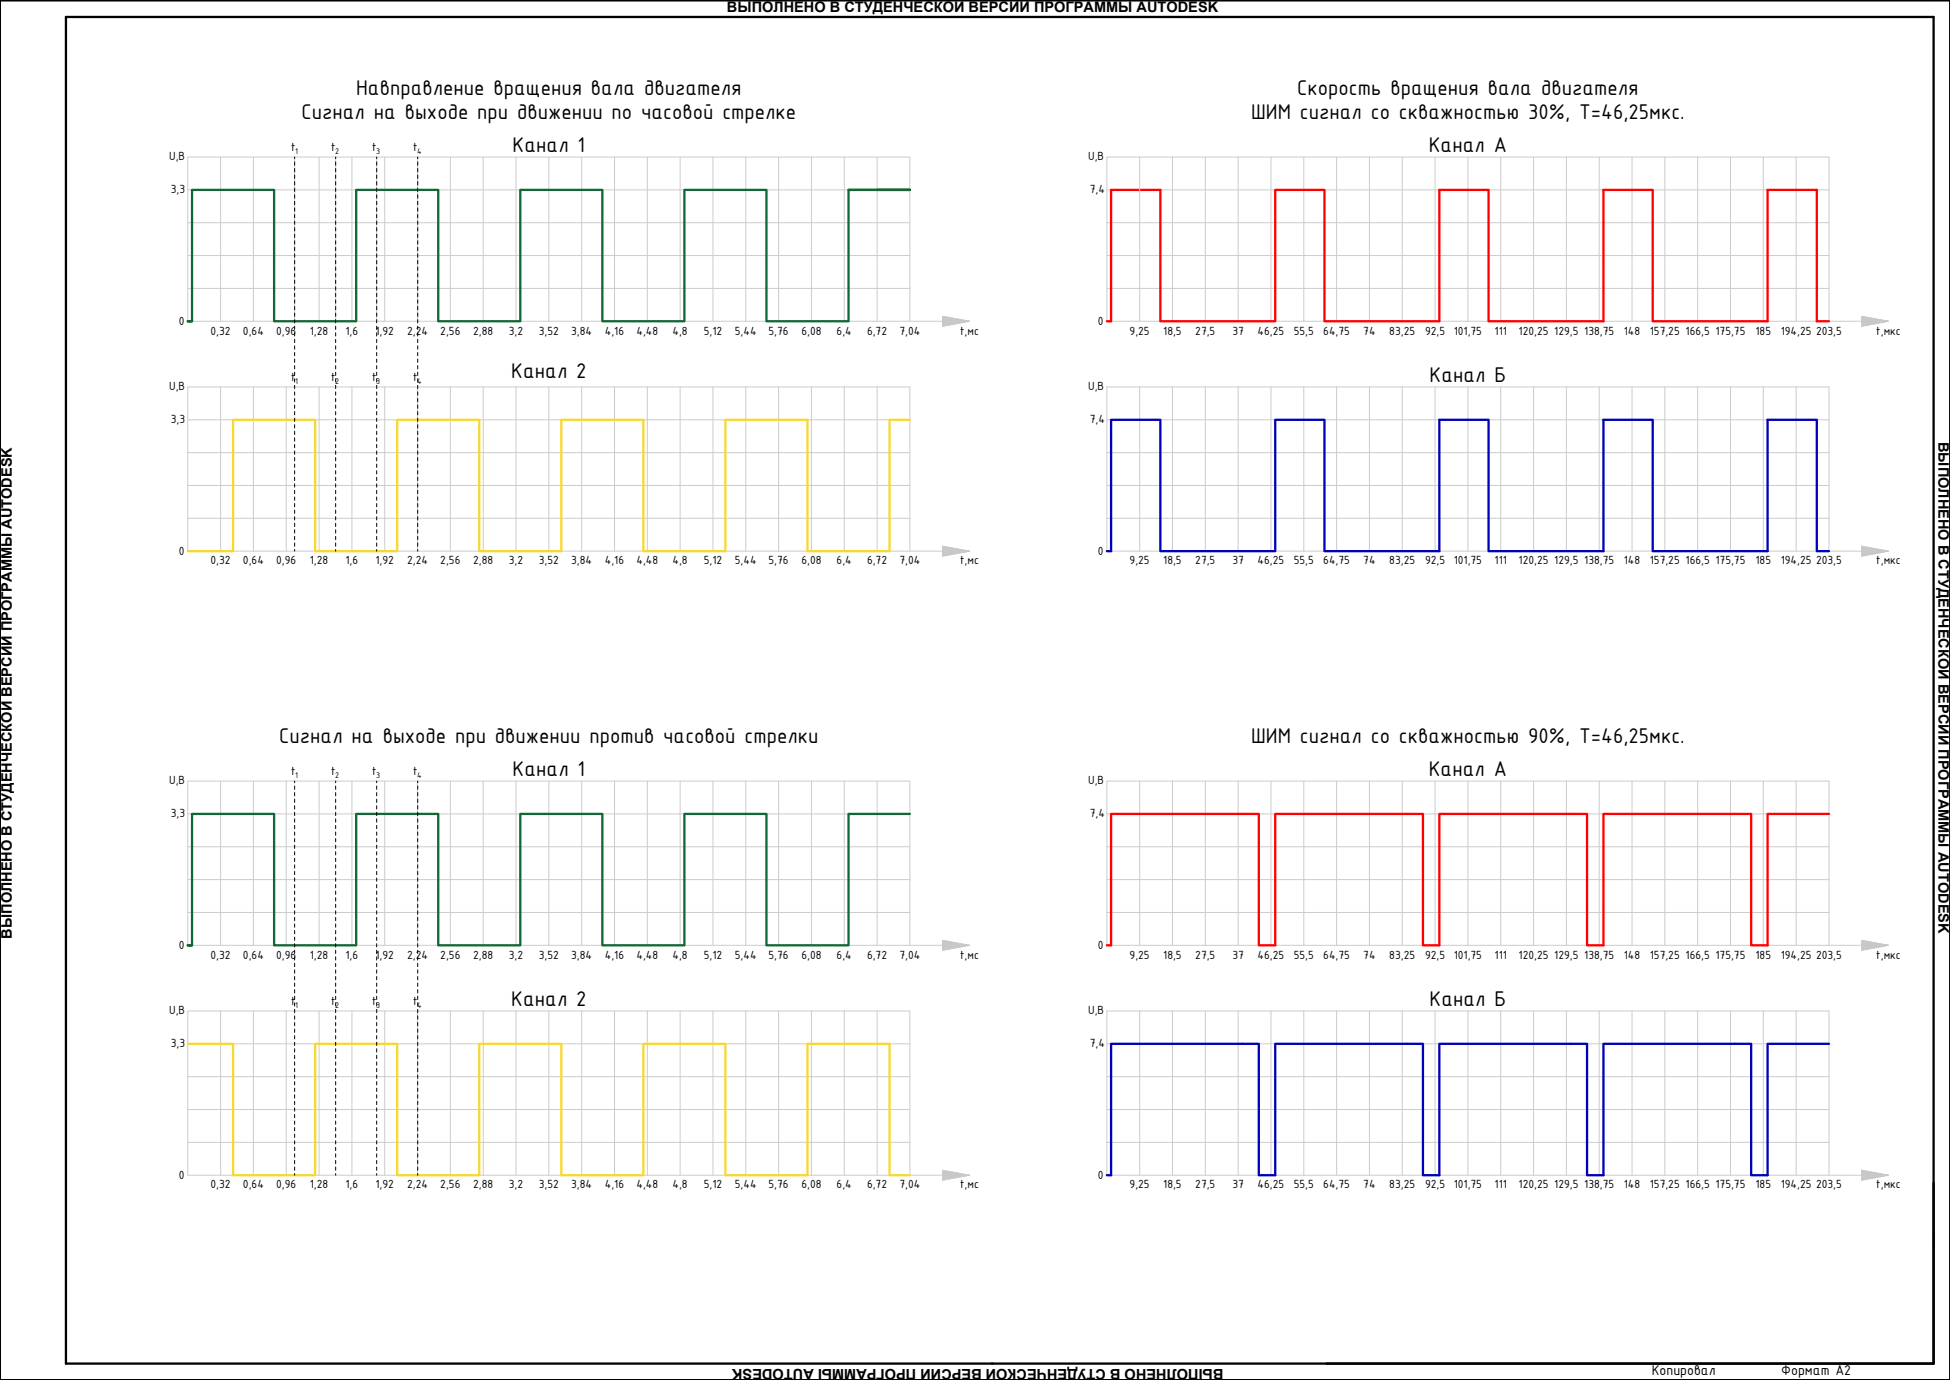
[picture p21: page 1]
Копировал; Формат A2 3,30; Скорость вращения вала двигателя ШИМ сигнал со скважностью 30%, T=46,25мкс. Навправление вращения вала двигателя Сигнал на выходе при движении по часовой стрелке; t,мкс t,мс; t,мкс 0,32 0,64 0,96; t,мкс 9,25; t,мкс Сигнал на выходе при движении против часовой стрелки; 6,72 7,04 Канал 1 Канал 1 Канал 2 Канал 2 t1; Канал А Канал Б Канал Б 3,30 U,В3,30 U,В3,30 U,В; ШИМ сигнал со скважностью 90%, T=46,25мкс. Канал А

ВЫПОЛНЕНО В СТУДЕНЧЕСКОЙ ВЕРСИИ ПРОГРАММЫ AUTODESK

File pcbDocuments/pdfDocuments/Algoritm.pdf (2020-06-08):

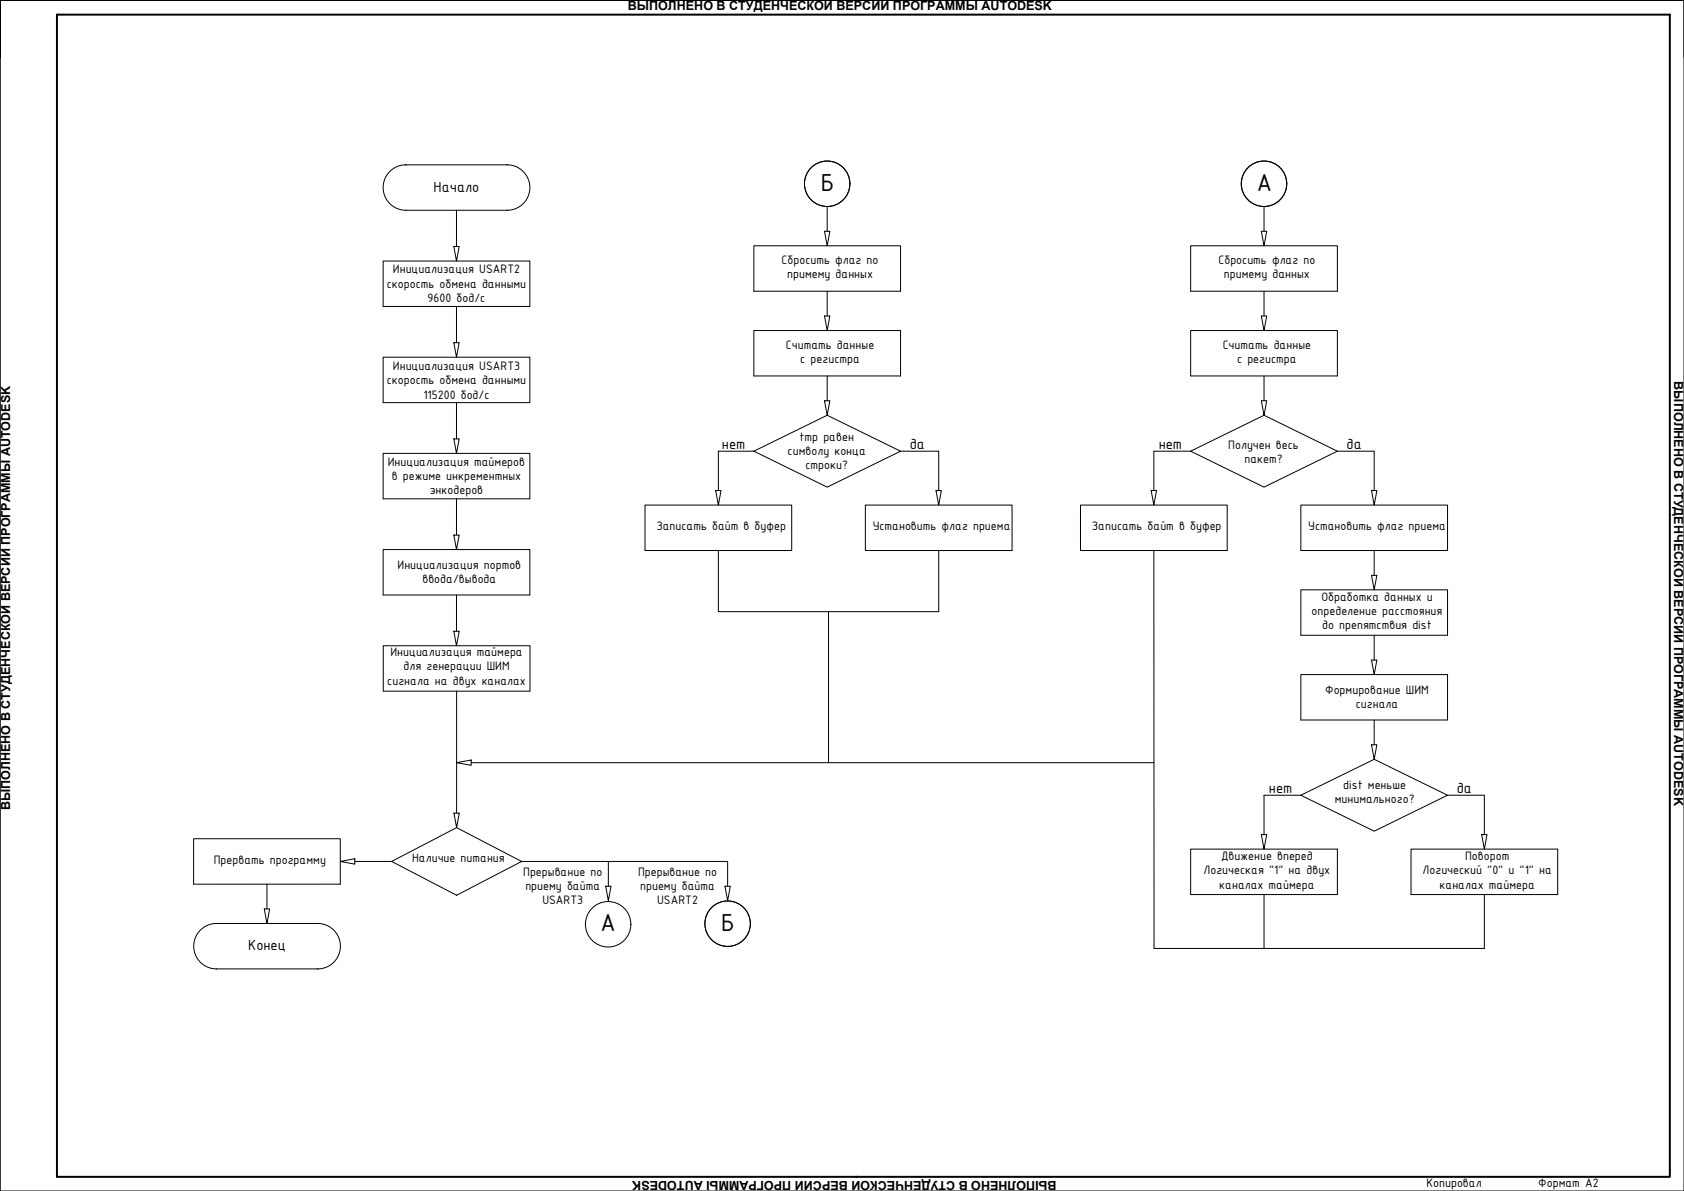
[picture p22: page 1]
Начало Инициализация USART2 скорость обмена данными 9600 бод/с Инициализация USART3 скорость обмена данными 115200 бод/с Инициализация таймеров в режиме инкрементных энкодеров Инициализация портов ввода/вывода Инициализация таймера для генерации ШИМ сигнала на двух каналах Наличие питания; Прерывание по приему байта USART3; Прерывание по приему байта USART2 Прервать программу Конец; Б Считать данные с регистра tmp равен символу конца строки? Записать байт в буфер; Установить флаг приема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

ВЫПОЛНЕНО В СТУДЕНЧЕСКОЙ ВЕРСИИ ПРОГРАММЫ AUTODESK

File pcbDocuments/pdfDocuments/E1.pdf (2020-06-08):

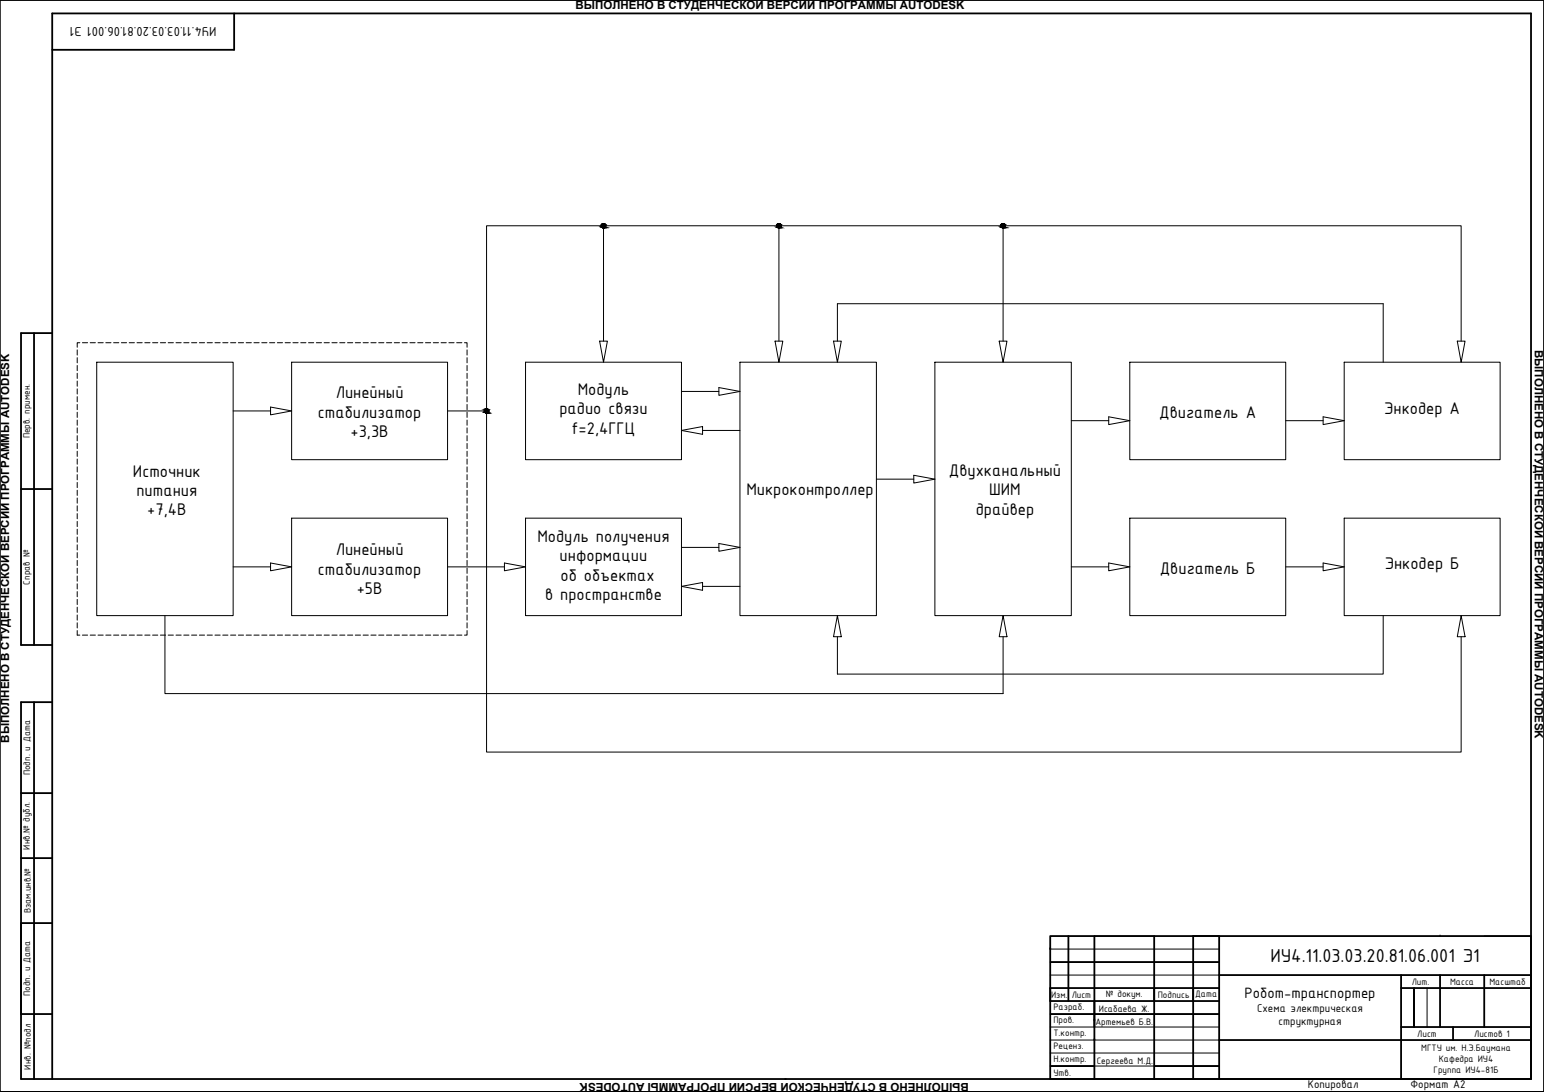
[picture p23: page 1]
Источник питания +7,4В; Линейный стабилизатор +3,3В Линейный стабилизатор +5В; Модуль радио связи f=2,4ГГЦ Модуль получения информации об объектах в пространстве; Микроконтроллер; Двухканальный ШИМ драйвер; Двигатель A; Энкодер A Двигатель Б; Энкодер Б Разраб. Пров. Изм.; Лист; № докум.; Подпись; Дата; Лит.; Масса; Масштаб Т.контр.; Листов 1 Реценз. Н.контр. Утв.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

ВЫПОЛНЕНО В СТУДЕНЧЕСКОЙ ВЕРСИИ ПРОГРАММЫ AUTODESK

Инв. №подл Подп. и Дата Взам.инв.№ Инв.№ дубл. Подп. и Дата Справ № Перв. примен. 1 Э 4.11.03.03.20.81.06.001 ИУ Исабаева Ж. Сергеева М.Д. Артемьев Б.В.

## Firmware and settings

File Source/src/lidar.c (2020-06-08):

#include "stm32f10x.h" 
#include "string.h"
#include <stdlib.h>


/* lidar begin */
//void usart2Begin(uint32_t baudrate) {
//	
//	uint32_t _BRR = 72000000 / (baudrate * 2);
//	
//	RCC->APB2ENR |= RCC_APB2ENR_AFIOEN; 
//	RCC->APB1ENR |= RCC_APB1ENR_USART2EN;
//	RCC->APB2ENR |= RCC_APB2ENR_IOPAEN;
//	
//	GPIOA->CRL &=~ (GPIO_CRL_CNF2 | GPIO_CRL_MODE2);
//	GPIOA->CRL |=  (GPIO_CRL_CNF2_1 | GPIO_CRL_MODE2_1); //TX
//	
//	GPIOA->CRL &=~ (GPIO_CRL_CNF3 | GPIO_CRL_MODE3); 
//	GPIOA->CRL |= GPIO_CRL_CNF3_0; // RX
//	
//	USART2->BRR = _BRR;
//	USART2->CR1 = 0x0;
//	USART2->CR2 = 0x0;
//	
//	USART2->CR1 |= USART_CR1_TE;
//	USART2->CR1 |= USART_CR1_RE;
//	USART2->CR1 |= USART_CR1_UE;
//	
//	USART2->CR1 |= USART_CR1_RXNEIE;
//	NVIC_EnableIRQ(USART2_IRQn);
//}

//char USART2_BUFFER[8];
//uint16_t i = 0;

//void USART2_IRQHandler(void) {
//	
//	if ((USART2->SR & USART_SR_RXNE) != 0) { 
//	  
//		char tmp = USART2->DR;
//		
//		if(tmp == 0x59) {
//			  i = 0;	
//			  memset(USART2_BUFFER, 0, 8);
//				USART2_BUFFER[i++] = tmp;
//		} else {
//				USART2_BUFFER[i++] = tmp;
//		}			
//	}
//}

//void usart2Transmission(char* str) {
//	
//	for(uint16_t i=0; i < strlen(str); i++) {
//		while(!(USART2->SR & USART_SR_TC));
//		USART2->DR = str[i];
//	}
//	
//	while(!(USART2->SR & USART_SR_TC));
//	USART2->DR = '\n';
//}

//void usart2TransmissionByte(uint8_t byte) {
//		while(!(USART2->SR & USART_SR_TC));
//		USART2->DR = byte;
//}

/* lidar end */


/* driver begin */

void pwmBegin(void) {
	RCC->APB1ENR |= RCC_APB1ENR_TIM2EN;
	RCC->APB2ENR |= RCC_APB2ENR_IOPAEN;
	
	GPIOA->CRL &=~ (GPIO_CRL_MODE0 | GPIO_CRL_CNF0);
	GPIOA->CRL |= (GPIO_CRL_CNF0_1 | GPIO_CRL_MODE0);
	
	GPIOA->CRL &=~ (GPIO_CRL_MODE1 | GPIO_CRL_CNF1);
	GPIOA->CRL |=  (GPIO_CRL_CNF1_1 | GPIO_CRL_MODE1);
		
	TIM2->PSC = 32; // 72000000 / 72 / 100 10k
	TIM2->ARR = 100;
	
	TIM2->CCR1 = 0; //CH1
	TIM2->CCR2 = 0; //CH2
	
	TIM2->CCMR1 |=  TIM_CCMR1_OC1M_1 | TIM_CCMR1_OC1M_2;
	TIM2->CCER  |=  TIM_CCER_CC1E;
	TIM2->CCER  &=~ TIM_CCER_CC1P;
	
	TIM2->CCMR1 |=  TIM_CCMR1_OC2M_1 | TIM_CCMR1_OC2M_2;
	TIM2->CCER  |=  TIM_CCER_CC2E;
	TIM2->CCER  &=~ TIM_CCER_CC2P;
	
	TIM2->CR1   &=~ TIM_CR1_DIR;
	TIM2->CR1   |=  TIM_CR1_CEN;
}

void driverBegin(void) {
	
	RCC->APB2ENR |= RCC_APB2ENR_IOPAEN;
	RCC->APB2ENR |= RCC_APB2ENR_IOPBEN;
	
	GPIOA->CRL &=~ (GPIO_CRL_MODE4 | GPIO_CRL_CNF4); //PA4 AIN2
	GPIOA->CRL |=   GPIO_CRL_MODE4;
	
	GPIOA->CRL &=~ (GPIO_CRL_MODE5 | GPIO_CRL_CNF5); //PA5 AIN1
	GPIOA->CRL |=   GPIO_CRL_MODE5;
	
	GPIOB->CRL &=~ (GPIO_CRL_MODE0 | GPIO_CRL_CNF0); //PB0 BIN1
	GPIOB->CRL |=   GPIO_CRL_MODE0;
	
	GPIOB->CRL &=~ (GPIO_CRL_MODE1 | GPIO_CRL_CNF1); //PB1 BIN2
	GPIOB->CRL |=   GPIO_CRL_MODE1;
}

void motorBegin(void) {
	pwmBegin();
	driverBegin();
}

void motorPwm(uint16_t left, uint16_t right) {
	TIM2->CCR1 = left;  //CH1
	TIM2->CCR2 = right; //CH2
}

void motorLeft(uint16_t pwm) {
	 motorPwm(pwm, pwm);
	 
	 GPIOA->BSRR = GPIO_BSRR_BR5; // AIN1 
	 GPIOA->BSRR = GPIO_BSRR_BS4; // AIN2
	 
	 GPIOB->BSRR = GPIO_BSRR_BS0; // BIN1
	 GPIOB->BSRR = GPIO_BSRR_BR1; // BIN2
}

void motorRight(uint16_t pwm) {
	 motorPwm(pwm, pwm);
	 
	 GPIOA->BSRR = GPIO_BSRR_BS5; // AIN1 
	 GPIOA->BSRR = GPIO_BSRR_BR4; // AIN2
	 
	 GPIOB->BSRR = GPIO_BSRR_BR0; // BIN1
	 GPIOB->BSRR = GPIO_BSRR_BS1; // BIN2
}

void motorForward(uint16_t pwm) {
	 motorPwm(pwm, pwm);
	 
	 GPIOA->BSRR = GPIO_BSRR_BS5; // AIN1 
	 GPIOA->BSRR = GPIO_BSRR_BR4; // AIN2
	 
	 GPIOB->BSRR = GPIO_BSRR_BS0; // BIN1
	 GPIOB->BSRR = GPIO_BSRR_BR1; // BIN2
}

void motorBack(uint16_t pwm) {
	 motorPwm(pwm, pwm);
	 
	 GPIOA->BSRR = GPIO_BSRR_BR5; // AIN1 
	 GPIOA->BSRR = GPIO_BSRR_BS4; // AIN2
	 
	 GPIOB->BSRR = GPIO_BSRR_BR0; // BIN1
	 GPIOB->BSRR = GPIO_BSRR_BS1; // BIN2
}

void motorStop() {
	 motorPwm(0, 0);
	 
	 GPIOA->BSRR = GPIO_BSRR_BR5; // AIN1 
	 GPIOA->BSRR = GPIO_BSRR_BR4; // AIN2
	 
	 GPIOB->BSRR = GPIO_BSRR_BR0; // BIN1
	 GPIOB->BSRR = GPIO_BSRR_BR1; // BIN2
}

/* driver end */

TIM_TypeDef * tim;


/* bluetooth begin */
void usart2Begin(uint32_t baudrate) {
	
	uint32_t _BRR = 72000000 / (baudrate * 2);
	
	RCC->APB2ENR |= RCC_APB2ENR_AFIOEN; 
	RCC->APB1ENR |= RCC_APB1ENR_USART2EN;
	RCC->APB2ENR |= RCC_APB2ENR_IOPAEN;
	
	GPIOA->CRL &=~ (GPIO_CRL_CNF2 | GPIO_CRL_MODE2);
	GPIOA->CRL |=  (GPIO_CRL_CNF2_1 | GPIO_CRL_MODE2_1); //TX
	
	GPIOA->CRL &=~ (GPIO_CRL_CNF3 | GPIO_CRL_MODE3); 
	GPIOA->CRL |= GPIO_CRL_CNF3_0; // RX
	
	USART2->BRR = _BRR;
	USART2->CR1 = 0x0;
	USART2->CR2 = 0x0;
	
	USART2->CR1 |= USART_CR1_TE;
	USART2->CR1 |= USART_CR1_RE;
	USART2->CR1 |= USART_CR1_UE;
	
	USART2->CR1 |= USART_CR1_RXNEIE;
	NVIC_EnableIRQ(USART2_IRQn);
}

char USART2_BUFFER[20];
uint16_t i = 0;
char string [20];

void usart2Receive(void) {
	if (!strcmp(USART2_BUFFER, "forward50\r")) {
      motorForward(50);
	}
	
	if (!strcmp(USART2_BUFFER, "forward80\r")) {
      motorForward(80);
	}
		
	if (!strcmp(USART2_BUFFER, "back\r")) {
      motorBack(50);
	}
	
	if (!strcmp(USART2_BUFFER, "right50\r")) {
      motorRight(30);
	    for(uint32_t i=0; i<1040000; i++);
	   	motorForward(30);
	}
	
	if (!strcmp(USART2_BUFFER, "left50\r")) {
      motorLeft(30);	
			for(uint32_t i=0; i<1040000; i++);
	   	motorForward(30);
	}
	
	if (!strcmp(USART2_BUFFER, "stop\r")) {
      motorStop();	
	}
	
	//for(uint32_t i=0; i<24000000; i++); 
	//motorStop();
}

void USART2_IRQHandler(void) {
	
	if ((USART2->SR & USART_SR_RXNE) != 0) { 
	  
		char tmp = USART2->DR;
		
		if(tmp == 0x0A) {
		  i = 0;	
			usart2Receive();
			memset(USART2_BUFFER, 0, 10);
			
		} else {
				USART2_BUFFER[i] = tmp;
			  string[i] = USART2_BUFFER[i];
			  i++;
		}			
	}
}

void usart2Transmission(char* str) {
	
	for(uint16_t i=0; i < strlen(str); i++) {
		while(!(USART2->SR & USART_SR_TC));
		USART2->DR = str[i];
	}
	
	while(!(USART2->SR & USART_SR_TC));
	USART2->DR = '\n';
}

void usart2TransmissionByte(uint8_t byte) {
		while(!(USART2->SR & USART_SR_TC));
		USART2->DR = byte;
}
/* bluetooth end */


int main() {

	motorBegin();

	volatile uint16_t speed = 30;

	usart2Begin(115200);
	
   	motorStop();
		for(uint32_t i=0; i<5000000; i++);  
		motorForward(speed);
		for(uint32_t i=0; i<15000000; i++); 
		
	  motorStop();
	  for(uint32_t i=0; i<1500000; i++);
	
		motorLeft(speed);
		for(uint32_t i=0; i<1300000; i++); 
	  
	  motorStop();
	  for(uint32_t i=0; i<100000; i++);
		
		motorForward(speed);
		for(uint32_t i=0; i<2500000; i++); 
		
		motorStop();
	  for(uint32_t i=0; i<1000000; i++);
		
		motorRight(speed);
		for(uint32_t i=0; i<1300000; i++); 
		
		motorStop();
	  for(uint32_t i=0; i<100000; i++);
		
		motorForward(speed);
		for(uint32_t i=0; i<7000000; i++);
		
		motorStop();
	  for(uint32_t i=0; i<1000000; i++);
		
		motorLeft(speed);
		for(uint32_t i=0; i<2900000; i++); 
		
		motorStop();
	  for(uint32_t i=0; i<1000000; i++);
		
		
		motorForward(speed);
		for(uint32_t i=0; i<21000000; i++);

		motorLeft(speed);
		for(uint32_t i=0; i<1600000; i++); 

//		motorForward(speed);
//		for(uint32_t i=0; i<3000000; i++); 
		
		motorStop();	
	while(1) { 
		
		

		
		
			
		usart2Transmission("Hi");
		
	}

}

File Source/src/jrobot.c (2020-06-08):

#include "motor.h"
#include "math.h"

TIM_TypeDef * tim;

void tim4Begin(void) {
	RCC->APB1ENR |= RCC_APB1ENR_TIM4EN;
	
	TIM4->PSC     = 72000000 / 1000000 - 1;
	TIM4->ARR     = 100;
	
	TIM4->DIER   |= TIM_DIER_UIE;
  TIM4->CR1	   |= TIM_CR1_CEN;
	
	NVIC_EnableIRQ(TIM4_IRQn);
}

int32_t volatile K = 100;
int32_t volatile delta = 0;
float   volatile encoder = 0;
uint32_t volatile left;
uint32_t volatile right;
float volatile diff = 0;


void TIM4_IRQHandler(void) {
	
	TIM4->SR &=~ TIM_SR_UIF;
		
	encoder = encoderRead(); 
	
	delta = K * (encoder + diff);
	
	left = 150 + delta;
	right = 150 - delta;
	
	if (left > 500)  left = 500;
	if (right > 500) right = 500;
	
	motorForward(left, right);
}

int main() {
	
	tim4Begin();
	
	tim = TIM1;
	
	encoderRightBegin();
	encoderLeftBegin();
	
	motorBegin();
		
	while(1) {
		
		
	
	}
	
}
